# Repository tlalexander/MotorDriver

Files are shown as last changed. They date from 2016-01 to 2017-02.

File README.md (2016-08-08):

# MotorDriver

This is a smart brushless motor driver board capable of precision servo-control (position and velocity control) of a low cost hobby brushless motor. This is managed by use of a magnetic angle sensor, and a feedback software that runs on the motor driver's onboard 64MHz ARM CPU.

The board is still under development, but the ultimate goal of this board is to enable lower cost robotics, especially for hobbyists.

Brushless motors have excellent torque characteristics, but complexity in their control has meant that complex gear reductions are typically needed to make use of these motors. With improved precision on motion control, larger motors can be used in lieu of complex gear trains, reducing system complexity.

Essentially, this board moves a mechanical problem to a software problem.

This is specifically quite helpful in the field of ultra low cost 3D printed robotics, where simpler mechanisms enable near zero cost robots to be built at home.

This board is designed to facilitate the development of these applications, but is not itself particularly low cost. If you like the idea of good quality brushless motor control for hobbyist robotics, please fork this project, simplify the design, and flood the market with cheap clones from China.

### Note 7/8/2016:
The current board design works with some changes. I haven't published the changes yet. If you want to make one, contact me first. I'd be happy to push the changes if someone wants to make some of these.

Features (planned)
------

* At least 1kW maximum power handling (depending on FETs used; theoretical max power for this FET package is 3kW).
* Current feedback for proper current-based motor control.
* Position feedback via external magentic encoder enables full closed loop control of low cost hobby brushless motors.
* Devices can be synchronized for six wire motor control (custom windings, linear motors, etc).
* Independent control of all bridges allows for brushed motor control with an additional half H bridge for other loads.
* USB interface allows easy control from a linux PC. Serial interface allows control from embedded systems such as Arduino.
* CPU runs Arduino code for easy portability.
* Multicolor LED to indicate status.

TODO
-----

* ~~Determine necessary device pinout and add properly wired headers.~~
* ~~Finish layout of current sense section.~~
* ~~Add jumper for battery power to CPU.~~
* ~~Full design review (is everything hooked up right?).~~
* ~~Finish all layout of Board V1.~~
* ~~Produce first test version.~~
* Full board test. (in progress)
* Write firmware for device.

Media
-----
It works! Check out the sweet video:
https://www.youtube.com/watch?v=cGBqlPRFbaQ

License
-----

This project is licensed under Creative Commons Attribution-ShareAlike 4.0 International (CC BY-SA 4.0), which is available at: http://creativecommons.org/licenses/by-sa/4.0/ If you use the files, please check them carefully - they may contain errors.

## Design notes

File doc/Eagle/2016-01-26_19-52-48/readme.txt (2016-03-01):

**********************************************************
*****************Schematic Instructions  *******************
**********************************************************

To import your new Schematic file into Eagle:

1. Unzip the downloaded folder files to local directory and Start Eagle.
2. Select "File"->"Open"->"Schematic..." from the menu at the top of
   the screen.
3. Browse to your newly exported file and select the ".sch" file extension.
4. You should now see your schamtic available in Eagle.

**********************************************************
*******************  PCB Instructions  *******************
**********************************************************

To import your new BOARD file into Eagle:

1. Unzip the downloaded folder files to local directory and Start Eagle.
2. Select "File"->"Open"->"Board..." from the menu at the top of
   the screen.
3. Browse to your newly exported file and select the ".brd" file extension.
4. Planes will need to be repoured to update the polygon fills
	1. Once your board is loaded, type "ratsnest" into the command
	   line and press the Enter key.
	2. The polygons should all be filled now.
5. You should now have an image of your board available in Eagle.

**********************************************************
*******************  LIB Instructions  *******************
**********************************************************

To import your new library into Eagle:

1. Start Eagle.
2. Select "File"->"New"->"Library" from the menu.
3. In the blank library window, select "File" -> "Execute Script"
   from the menu.
5. Browse to your newly exported Eagle Script file (".scr" file extension)
6. After opening the file, the script will populate the new library.
   Layer 93 should NOT exist.
7. Use "File"->"Save" (or "Save As..") to save the library to the desired
   location in Eagle native format.

For additional information, please visit this site:
http://www.accelerated-designs.com/help/Eagle_import.html

You may also find this video helpful:
http://youtu.be/5jGuWY-Yy3Q

**********************************************************
**********************************************************
**********************************************************

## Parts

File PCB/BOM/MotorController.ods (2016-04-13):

Qty | Value | Device | Package | Parts | Digikey | Description | CAP | DATASHEETURL | MANUFACTURER_NAME | MANUFACTURER_PART_NUMBER | MOUNTTYPE | PACKAGEREFERENCE | PARTNUMBER | PIN_COUNT | POWER | PROD_ID | REFDES | RESISTANCE | ROHS | TOLERANCE | TYPE | VALUE | VDC | VENDOR | VFATIO | VRRM
6 | M20 | M20 | 1X20 | JP13, JP14, JP15, JP16, JP17, JP18 |  | This is just like the LOCK variant in that the holes are staggared by 5 mil, but except for the last two holes. They are not altered from the "standard" footprint layout. This is used for a special purpose on the layout of our Graphic LCD Backpack. Make sure you want to use this device before selecting it for you project!
2 | 04-JST-B4B-XH-A | 04-JST-B4B-XH-A | B4B-XH | X2, X4 | 455-2249-ND | JST CONNECTOR
3 | 05-JST-B5B-XH-A | 05-JST-B5B-XH-A | B5B-XH | X1, X6, X7 | 455-2270-ND | JST CONNECTOR
1 | 100nF | GRM188R72A104KA35D | CAP-0603 | CBOOT | 490-3285-1-ND |  | 0.0000001 |  | MuRata | GRM188R72A104KA35D |  |  |  |  |  |  |  |  |  |  |  |  | 100 | MuRata
1 | 470pF | CAPACITOR0603-CAP | CAP-0603 | U$5 | 490-1367-1-ND
4 | 0.22uF | CAPACITOR0805 | CAP-0805 | U$7, U$15, U$16, U$17 | 399-8049-1-ND
1 | 10uF | CAPACITOR0805 | CAP-0805 | U$4 | 587-1312-1-ND
1 | 4.7uF | GRM21BR61E475MA12L | CAP-0805 | COUT | 490-5422-1-ND |  | 0.0000047 | http://www.murata.com/products/catalog/pdf/c02e.pdf | MuRata | GRM21BR61E475MA12L |  |  |  |  |  |  |  |  |  |  |  |  | 25 | MuRata
1 | 2.2uF | C3225X7R2A225K230AB | CAP-1210 | CIN | 445-4497-1-ND |  | 0.0000022 | http://product.tdk.com/capacitor/mlcc/en/documents/mlcc%5Fcommercial%5Fmidvoltage%5Fen.pdf | TDK | C3225X7R2A225K230AB |  |  |  |  |  |  |  |  |  |  |  |  | 100 | TDK
2 |  | CAPACITOR-POLARIZED | CAP-6.5X18MM | C1, C4 | 4049PHCT-ND
1 | Value | LMR16006YDDCR | DDC0006A | U1 | 296-40294-1-ND |  |  |  | Texas Instruments | LMR16006YDDCR | SMT | DDC0006A | LMR16006YDDC | 6 |  |  | RefDes |  | Y |  | TYPE | Value
1 | 82uH | ME3220-823KLB | ME3220 | L1 |  |  |  |  | Coilcraft | ME3220-823KLB |  |  |  |  |  |  |  |  |  |  |  |  |  | Coilcraft
2 |  | RESISTOROHMITE | OHMITE_FCSL64_CURRENT_SENSE_RESISTOR | R2, R3 | FCSL64R050FERCT-ND | Resistor
1 | 770mV | DFLS1100-7 | POWERDI123 | D2 | DFLS1100DICT-ND |  |  | http://www.diodes.com/datasheets/ds30497.pdf | Diodes Inc. | DFLS1100-7 |  |  |  |  |  |  |  |  |  |  |  |  |  | Diodes Inc. | 0.77 | 100
6 | MOSFETSO-8 | MOSFETSO-8 | POWERPAK_S0-8 | AH, AL, BH, BL, CH, CL | SI7148DP-T1-E3CT-ND
6 | 4.7 | RESISTOR0402 | RES-0402 | R13, R14, R15, R16, R17, R18 | 311-4.70LRCT-ND | Resistor
6 | 33 | RESISTOR0402 | RES-0402 | R7, R8, R9, R10, R11, R12 | P33.0LCT-ND | Resistor
1 | 6.04k | CRCW04026K04FKED | RES-0402 | RFBB | 541-6.04KLCT-ND |  |  |  | Vishay-Dale | CRCW04026K04FKED |  |  |  |  | 0.063 |  |  | 6040 |  | 1 |  |  |  | Vishay-Dale
1 | 88.7k | CRCW040288K7FKED | RES-0402 | RFBT | 541-88.7KLCT-ND |  |  |  | Vishay-Dale | CRCW040288K7FKED |  |  |  |  | 0.063 |  |  | 88700 |  | 1 |  |  |  | Vishay-Dale
1 | 0R | RESISTOR0603 | RES-0603 | R1 | 311-0.0GRCT-ND | Resistor
6 |  | DIODESMA | SMA-DIODE | D1, D3, D4, D5, D6, D7, D8, D9, D10, D11, D12, D13 | SS110-TPCT-ND | Diode
1 | KMZ60_MAG_ANGLE_SENSOR | KMZ60_MAG_ANGLE_SENSOR | SO-8 | U$6 | 568-8400-1-ND
1 | OPA333D | OPA333D | SO08 | IC1 | 296-41364-1-ND | 1.8V, microPOWER CMOS OPERATIONAL AMPLIFIERS Zerø-Drift Series
1 | HIP4086_HEX_MOSFET_DRIVER | HIP4086_HEX_MOSFET_DRIVER | SOIC-24 | U$3 | HIP4086ABZ-ND
4 | STAND-OFF | STAND-OFF | STAND-OFF | STANDOFF1, STANDOFF2, STANDOFF3, STANDOFF4 |  | #4 Stand Off
14 | TEST_POINT5015KCT-ND | TEST_POINT5015KCT-ND | TEST_POINT_SMT_KEYSTONE_5015 | TP1, TP2, TP3, TP4, TP5, TP6, TP7, TP8, TP9, TP11, TP12, TP13, TP14, TP15 | 36-5015CT-ND | 36-5015CT-ND
1 | USBPTH | USBPTH | USB-B-PTH | X5 |  | USB Connectors

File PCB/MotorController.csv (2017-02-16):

Qty | Value | Device | Package | Parts | Description | CAP | COMPTYPE | DATASHEETURL | DCR | ESR | IDC | IO | IRMS | L | MANUFACTURER | MANUFACTURER_NAME | MANUFACTURER_PART_NUMBER | MOUNTTYPE | PACKAGEREFERENCE | PARTNUMBER | PIN_COUNT | POWER | PROD_ID | REFDES | RESISTANCE | ROHS | TOLERANCE | TYPE | VALUE | VDC | VENDOR | VFATIO | VRRM
2 |  | CAPACITOR-POLARIZED | CAP-6.5X18MM | C1, C4
6 |  | DIODESMA | SMA-DIODE | D1, D3, D4, D5, D6, D7 | Diode
1 |  | DIODESOD123 | SOD-123 | D14 | Diode
1 |  | M01PTH | 1X01 | J1 | Header 1
1 |  | M02PTH | 1X02 | J2 | Standard 2-pin 0.1 header. Use with"
2 |  | RESISTOR0603 | 0603-RES | R22, R23 | Resistor
2 |  | RESISTOROHMITE | OHMITE_FCSL64_CURRENT_SENSE_RESISTOR | R2, R3 | Resistor
3 | 0.22uF | CAPACITOR0805 | 0808-CAP | U$15, U$16, U$17
2 | 04-JST-B4B-XH-A | 04-JST-B4B-XH-A | B4B-XH | X2, X4 | JST CONNECTOR
2 | 05-JST-B5B-XH-A | 05-JST-B5B-XH-A | B5B-XH | X1, X7 | JST CONNECTOR
1 | 0R | RESISTOR0603 | 0603-RES | R1 | Resistor
1 | 100nF | GRM188R72A104KA35D | 0603 | CBOOT |  | 1.0E-7 |  |  |  | 0.0 |  |  | 0.0 |  |  | MuRata | GRM188R72A104KA35D |  |  |  |  |  |  |  |  |  |  |  |  | 100.0 | MuRata
1 | 10uF | CAPACITOR0805 | 0808-CAP | U$4
1 | 2.2uF | C3225X7R2A225K230AB | 1210 | CIN |  | 2.2E-6 |  | http://product.tdk.com/capacitor/mlcc/en/documents/mlcc%5Fcommercial%5Fmidvoltage%5Fen.pdf |  | 0.0028 |  |  | 9.824718 |  |  | TDK | C3225X7R2A225K230AB |  |  |  |  |  |  |  |  |  |  |  |  | 100.0 | TDK
3 | 20k | RESISTOR0402 | 0402-RES | R19, R20, R21 | Resistor
6 | 33 | RESISTOR0402 | 0402-RES | R7, R8, R9, R10, R11, R12 | Resistor
3 | 4.7 | RESISTOR0402 | 0402-RES | R13, R14, R15 | Resistor
1 | 4.7uF | GRM21BR61E475MA12L | 0805 | COUT |  | 4.7E-6 |  | http://www.murata.com/products/catalog/pdf/c02e.pdf |  | 0.0020 |  |  | 7.29 |  |  | MuRata | GRM21BR61E475MA12L |  |  |  |  |  |  |  |  |  |  |  |  | 25.0 | MuRata
1 | 470pF | CAPACITOR0603-CAP | 0603-CAP | U$5
1 | 6.04k | CRCW04026K04FKED | 0402 | RFBB |  |  |  |  |  |  |  |  |  |  |  | Vishay-Dale | CRCW04026K04FKED |  |  |  |  | 0.063 |  |  | 6040.0 |  | 1.0 |  |  |  | Vishay-Dale
1 | 6.04k | RESISTOR0402 | 0402-RES | R18 | Resistor
1 | 770mV | DFLS1100-7 | POWERDI123 | D2 |  |  |  | http://www.diodes.com/datasheets/ds30497.pdf |  |  |  | 1.0 |  |  |  | Diodes Inc. | DFLS1100-7 |  |  |  |  |  |  |  |  |  |  |  |  |  | Diodes Inc. | 0.77 | 100.0
1 | 7805TV | 7805TV | TO220V | IC2 | Positive VOLTAGE REGULATOR
1 | 82uH | ME3220-823KLB | ME3220 | L1 |  |  |  |  | 3.0 |  | 0.34 |  |  | 8.2E-5 |  | Coilcraft | ME3220-823KLB |  |  |  |  |  |  |  |  |  |  |  |  |  | Coilcraft
1 | 88.7K | RESISTOR0402 | 0402-RES | R17 | Resistor
1 | 88.7k | CRCW040288K7FKED | 0402 | RFBT |  |  |  |  |  |  |  |  |  |  |  | Vishay-Dale | CRCW040288K7FKED |  |  |  |  | 0.063 |  |  | 88700.0 |  | 1.0 |  |  |  | Vishay-Dale
1 | DNS | RESISTOR0402 | 0402-RES | R16 | Resistor
1 | DNS | RESISTOR0603 | 0603-RES | R4 | Resistor
1 | FILT_C | CAP0805 | 0805 | R6 | Capacitor
1 | FILT_R | RESISTOR0603 | 0603-RES | R5 | Resistor
5 | HIGHCURRENTPAD2 | HIGHCURRENTPAD2 | HIGH_CURRENT_PAD2 | +, -, A, B, C
1 | HIP4086_HEX_MOSFET_DRIVER | HIP4086_HEX_MOSFET_DRIVER | SOIC-24 | U$3
6 | M20 | M20 | 1X20 | JP13, JP14, JP15, JP16, JP17, JP18 | This is just like the LOCK variant in that the holes are staggared by 5 mil, but except for the last two holes. They are not altered from the standard" footprint layout. This is used for a special purpose on the layout of our Graphic LCD Backpack. Make sure you want to use this device before selecting it for you project!"
6 | MBRA140 | DIODE-SCHOTTKY-MBRA140 | SMA-DIODE | D8, D9, D10, D11, D12, D13 | Schottky diodes in SFE's production catalog |  |  |  |  |  |  |  |  |  |  |  |  |  |  |  |  |  | DIO-08053 |  |  |  |  |  | MBRA140
6 | MOSFETSO-8 | MOSFETSO-8 | POWERPAK_S0-8 | AH, AL, BH, BL, CH, CL
1 | MOSFETSOT23 | MOSFETSOT23 | SOT23 | U$1
1 | OPA333D | OPA333D | SO08 | IC1 | 1.8V, microPOWER CMOS OPERATIONAL AMPLIFIERS Zerø-Drift Series
1 | SOLDERJUMPERNO | SOLDERJUMPERNO | SJ_2S-NO | SJ1 | Solder Jumper
4 | STAND-OFF | STAND-OFF | STAND-OFF | STANDOFF1, STANDOFF2, STANDOFF3, STANDOFF4 | #4 Stand Off
14 | TEST_POINT5015KCT-ND | TEST_POINT5015KCT-ND | TEST_POINT_SMT_KEYSTONE_5015 | TP1, TP2, TP3, TP4, TP5, TP6, TP7, TP8, TP9, TP11, TP12, TP13, TP14, TP15 | Test Points. First one is Keystone
1 | USBPTH | USBPTH | USB-B-PTH | X5 | USB Connectors
1 | Value | LMR16006YDDCR | DDC0006A | U1 |  |  | IC |  |  |  |  |  |  |  | Texas Instruments | Texas Instruments | LMR16006YDDCR | SMT | DDC0006A | LMR16006YDDC | 6 |  |  | RefDes |  | Y |  | TYPE | Value

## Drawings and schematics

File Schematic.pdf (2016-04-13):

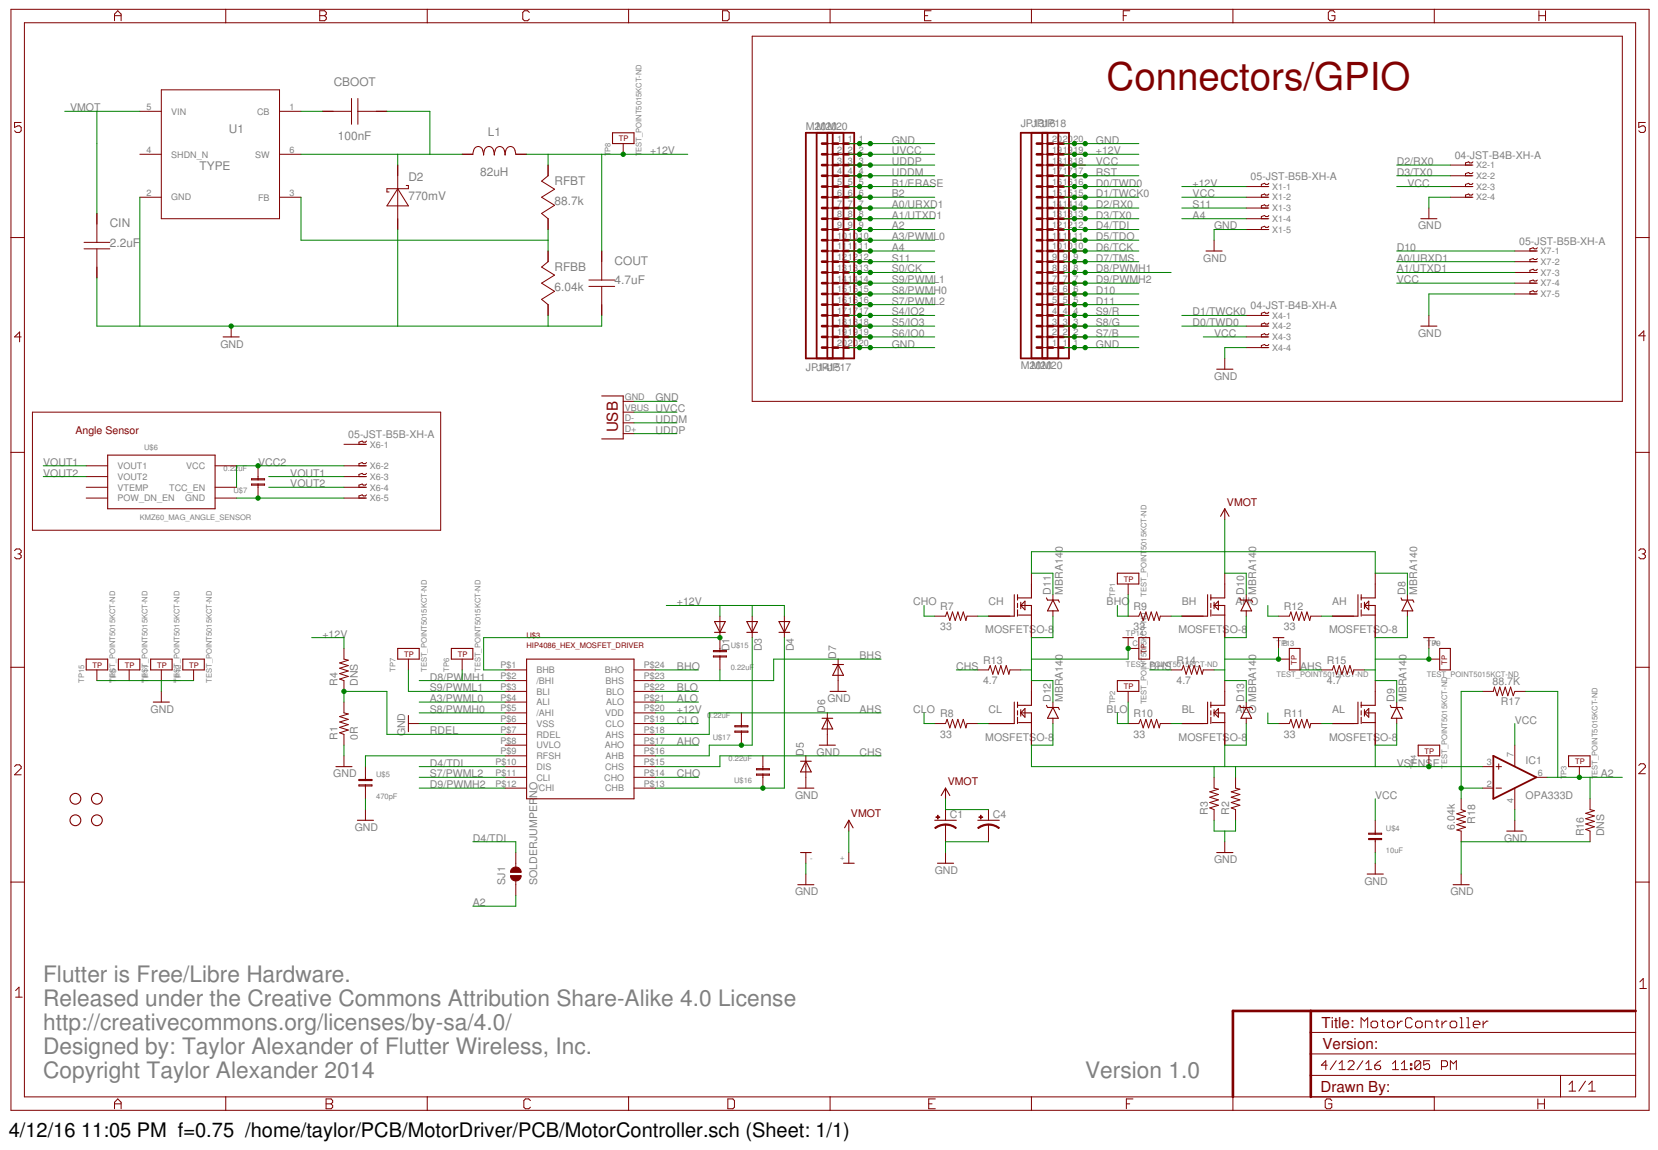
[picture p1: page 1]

Flutter is Free/Libre Hardware. Released under the Creative Commons Attribution Share-Alike 4.0 License
http://creativecommons.org/licenses/by-sa/4.0/

Drawn By: Title: Version:

4/12/16 11:05 PM f=0.75 /home/taylor/PCB/MotorDriver/PCB/MotorController.sch (Sheet: 1/1)

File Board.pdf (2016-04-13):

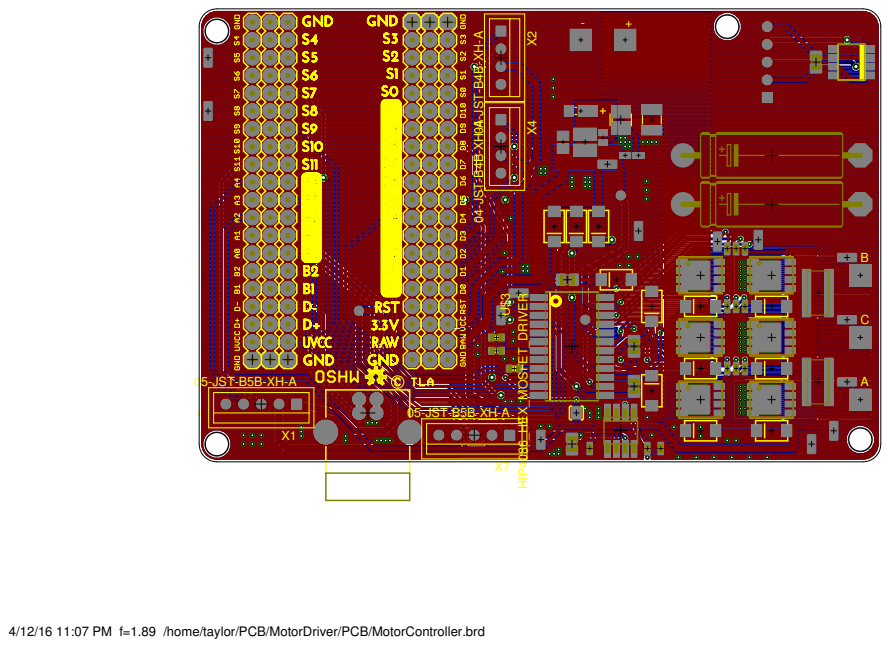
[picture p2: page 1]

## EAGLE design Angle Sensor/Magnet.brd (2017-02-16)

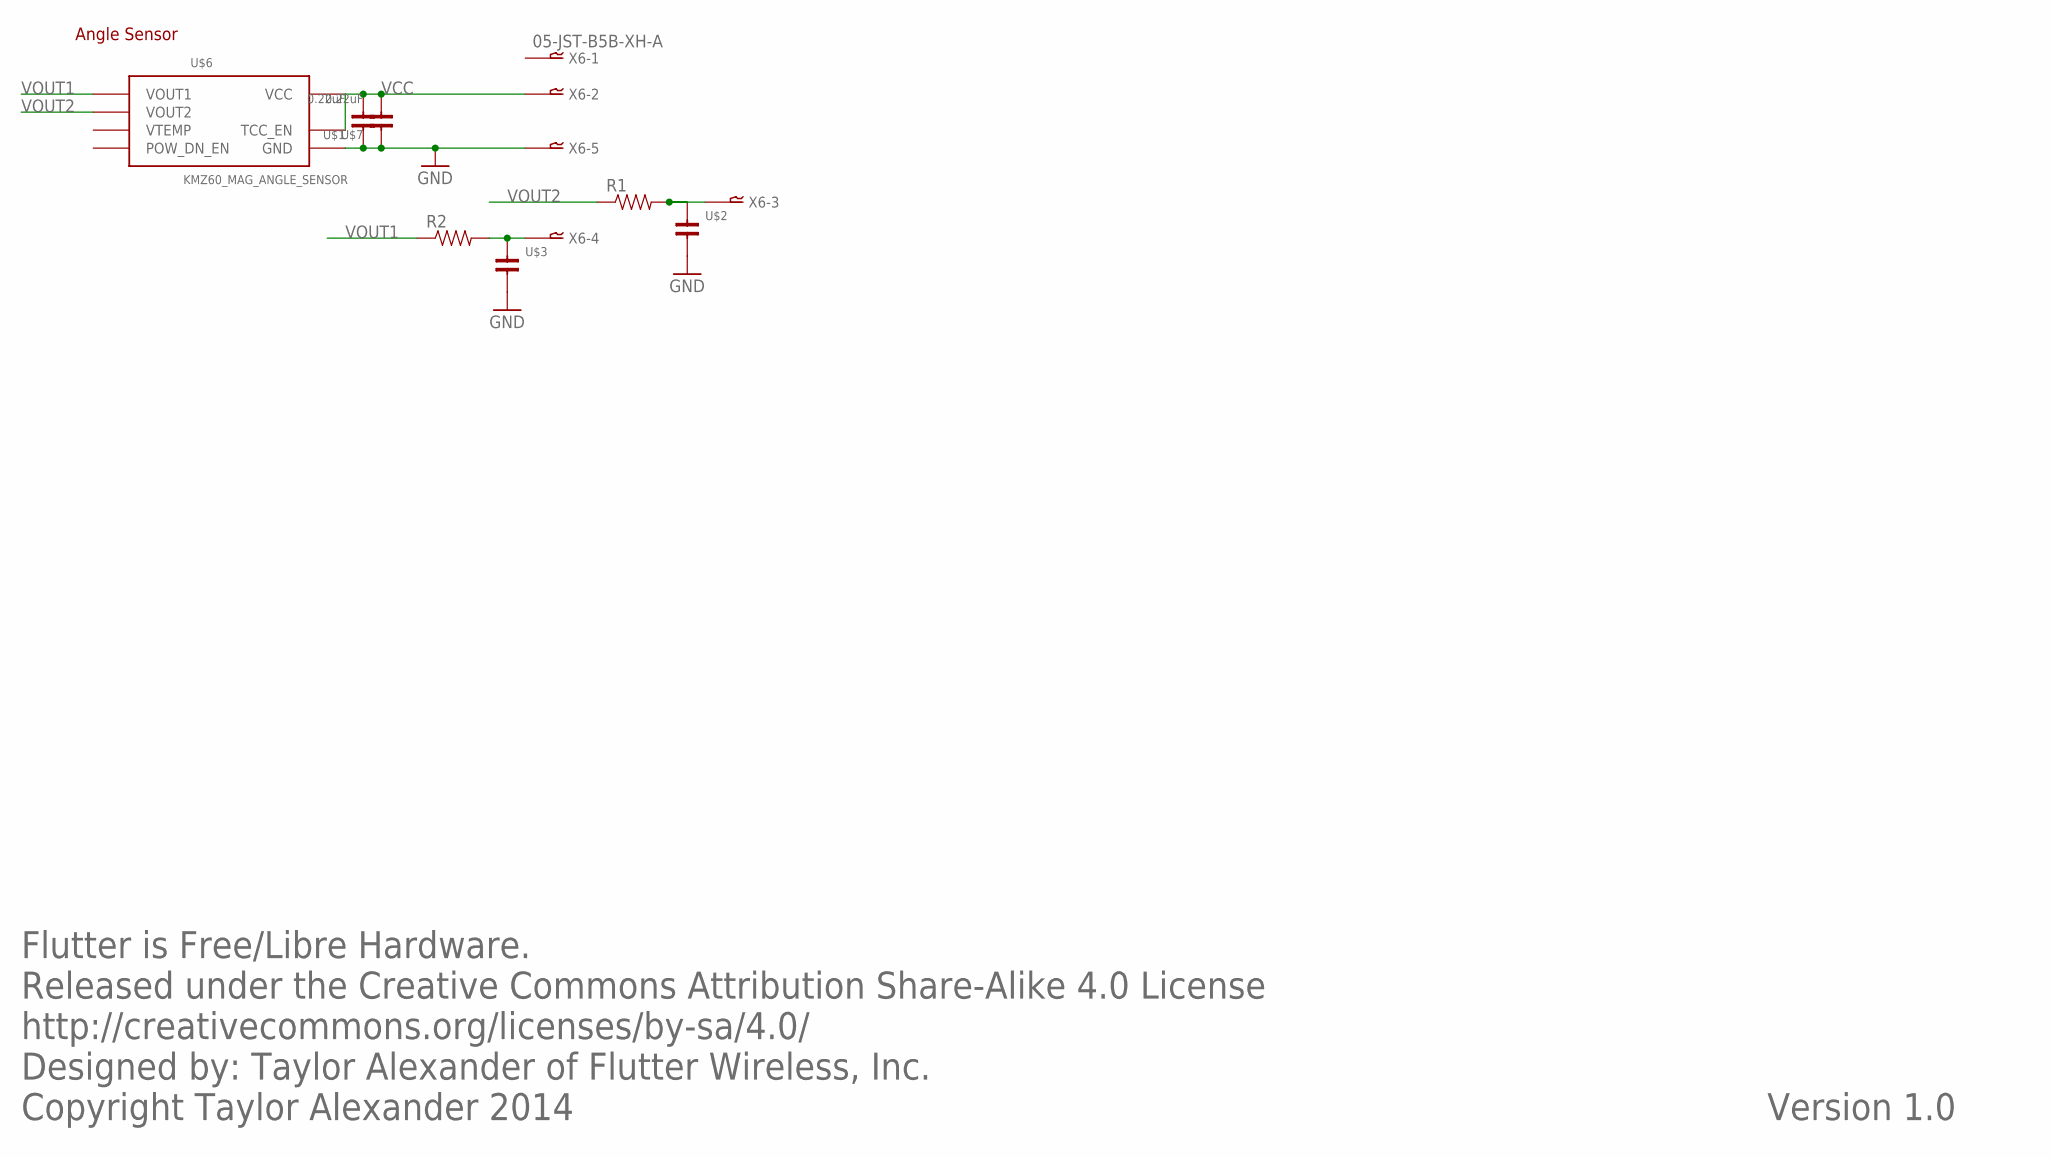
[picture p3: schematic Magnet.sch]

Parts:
R1, R2: RESISTOR0603; 0603-RES
U$1, U$7: 0.22uF; 0808-CAP
U$2, U$3: CAPACITOR0603-CAP; 0603-CAP
U$6: KMZ60_MAG_ANGLE_SENSOR; SO-8
X6: 05-JST-B5B-XH-A; B5B-XH

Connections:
GND: U$1.1, U$2.2, U$3.2, U$6.P$3 (GND), U$6.P$6 (GND), U$7.1, X6.P$5
unnamed: R2.2, U$3.1, X6.P$4
unnamed: R1.2, U$2.1, X6.P$3
VCC: U$1.2, U$6.P$1 (TCC_EN), U$6.P$7 (VCC), U$7.2, X6.P$2
VOUT1: R2.1, U$6.P$2 (VOUT1)
VOUT2: R1.1, U$6.P$4 (VOUT2)

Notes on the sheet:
Flutter is Free/Libre Hardware. Released under the Creative Commons Attribution Share-Alike 4.0 License http://creativecommons.org/licenses/by-sa/4.0/ Designed by: Taylor Alexander of Flutter Wireless, Inc. Copyright Taylor Alexander 2014
Version 1.0
Angle Sensor

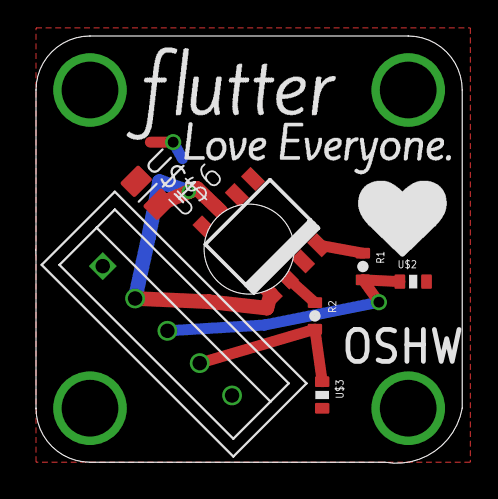
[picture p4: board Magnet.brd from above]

Board: 2 copper layers, 23.7 x 23.7 mm, 8 parts (1 on the bottom side), 6 nets.

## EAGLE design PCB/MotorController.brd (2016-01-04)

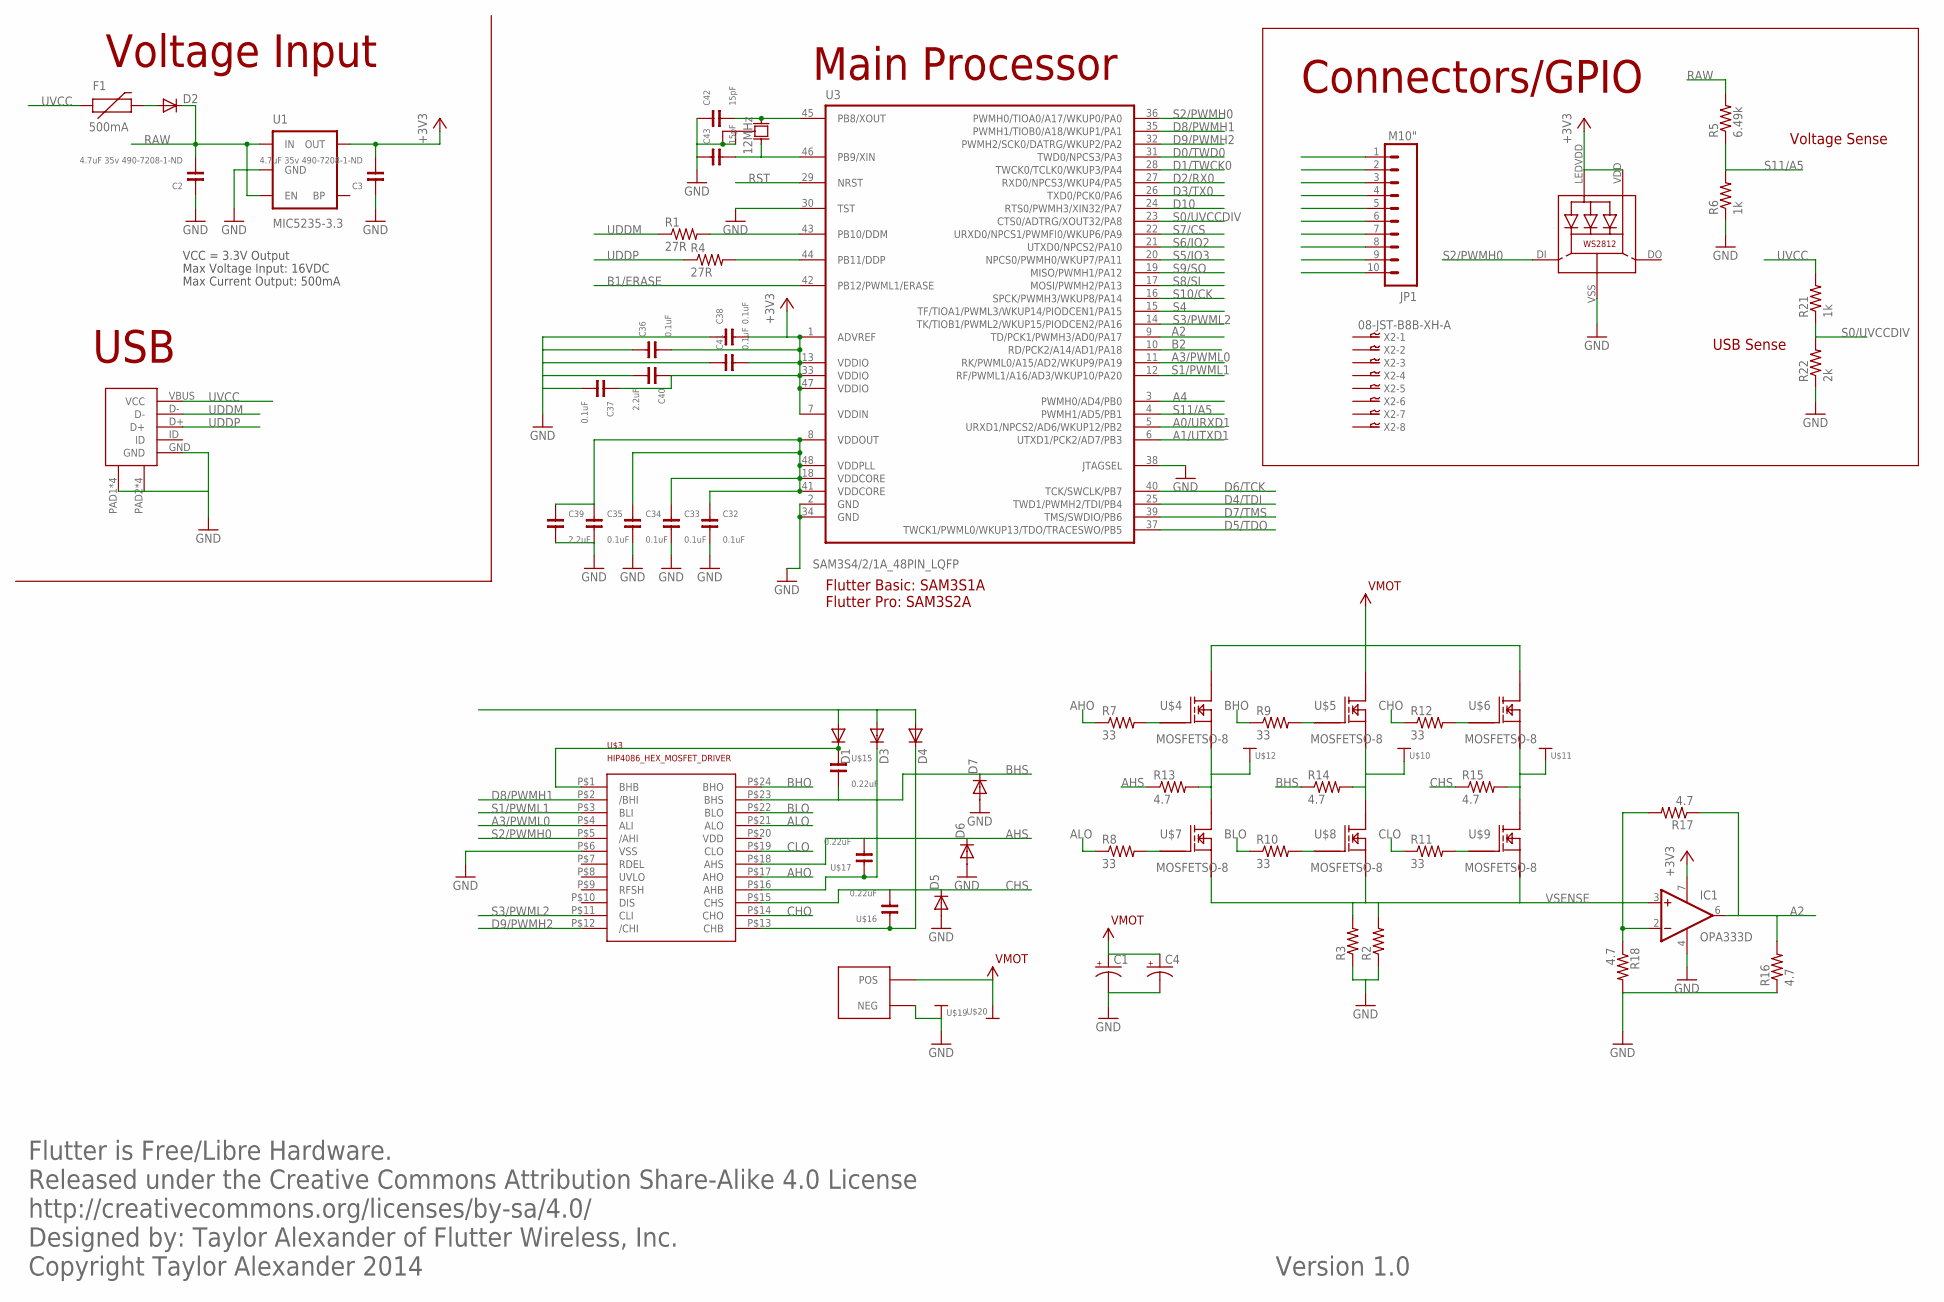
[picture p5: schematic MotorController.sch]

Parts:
C1, C4: CAPACITOR-POLARIZED; CAP-6.5X18MM
C2, C3: 4.7uF 35v 490-7208-1-ND; 0808-CAP
C32, C33, C34, C35, C36, C37, C38, C41: 0.1uF; 0402-CAP
C39, C40: 2.2uF; 0402-CAP
C42, C43: 15pF; 0402-CAP
D1, D3, D4, D5, D6, D7: DIODESMA; SMA-DIODE
D2: DIODESOD; SOD-323
F1: 500mA; 0603-PTC
IC1: OPA333D; SO08
JP1: M10"; 1X10
LED1: WS2812
R1, R4: 27R; 0402-RES
R2, R3: RESISTOROHMITE; OHMITE_FCSL64_CURRENT_SENSE_RESISTOR
R5: 6.49k; 0402-RES
R6, R21: 1k; 0402-RES
R7, R8, R9, R10, R11, R12: 33; 0402-RES
R13, R14, R15, R16, R17, R18: 4.7; 0402-RES
R22: 2k; 0402-RES
U1: MIC5235-3.3; SOT23-5
U3: SAM3S4/2/1A_48PIN_LQFP; LQFP48
U$2: MICRO_USB; MICRO-USB-SLOT-2
U$3: HIP4086_HEX_MOSFET_DRIVER; SOIC-24
U$4, U$5, U$6, U$7, U$8, U$9: MOSFETSO-8; POWERPAK_S0-8
U$10, U$11, U$12, U$19, U$20: HIGHCURRENTPAD2; HIGH_CURRENT_PAD2
U$15, U$16, U$17: 0.22uF; 0808-CAP
U$21: XT60; XT60_CONNECTOR
X1: 12MHz; XTAL_ABRACON_ABM8G_3.2MMX2.5MM
X2: 08-JST-B8B-XH-A; B8B-XH

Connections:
3.3V: C3.2, C36.2, C37.1, C38.2, C40.1, C41.2, U1.5 (OUT), U3.1 (ADVREF), U3.7 (VDDIN), U3.13 (VDDIO), U3.33 (VDDIO), U3.47 (VDDIO)
+1.8V: C32.1, C33.1, C34.1, C35.1, C39.1, U3.8 (VDDOUT), U3.18 (VDDCORE), U3.41 (VDDCORE), U3.48 (VDDPLL)
+3V3: IC1.7 (V+), LED1.LEDVDD, LED1.VDD
A: R15.2, U$6.S@1 (S), U$6.S@2 (S), U$6.S@3 (S), U$9.D@1 (D), U$9.D@2 (D), U$9.D@3 (D), U$9.D@4 (D), U$9.DTOP (D), U$11.P$1
A0/URXD1: U3.5 (URXD1/NPCS2/AD6/WKUP12/PB2)
A1/UTXD1: U3.6 (UTXD1/PCK2/AD7/PB3)
A2: IC1.6 (OUT), R16.2, R17.1, U3.9 (TD/PCK1/PWMH3/AD0/PA17)
A3/PWML0: U3.11 (RK/PWML0/A15/AD2/WKUP9/PA19), U$3.P$4 (ALI)
A4: U3.3 (PWMH0/AD4/PB0)
AHO: R7.1, U$3.P$17 (AHO)
AHS: D6.C, R13.1, U$3.P$18 (AHS), U$17.2
ALO: R8.1, U$3.P$21 (ALO)
B: R13.2, U$4.S@1 (S), U$4.S@2 (S), U$4.S@3 (S), U$7.D@1 (D), U$7.D@2 (D), U$7.D@3 (D), U$7.D@4 (D), U$7.DTOP (D), U$12.P$1
B1/ERASE: U3.42 (PB12/PWML1/ERASE)
B2: U3.10 (RD/PCK2/A14/AD1/PA18)
BHO: R9.1, U$3.P$24 (BHO)
BHS: D7.C, R14.1, U$3.P$23 (BHS), U$15.2
BLO: R10.1, U$3.P$22 (BLO)
C: R14.2, U$5.S@1 (S), U$5.S@2 (S), U$5.S@3 (S), U$8.D@1 (D), U$8.D@2 (D), U$8.D@3 (D), U$8.D@4 (D), U$8.DTOP (D), U$10.P$1
CHO: R12.1, U$3.P$14 (CHO)
CHS: D5.C, R15.1, U$3.P$15 (CHS), U$16.2
CLO: R11.1, U$3.P$19 (CLO)
D0/TWD0: U3.31 (TWD0/NPCS3/PA3)
D1/TWCK0: U3.28 (TWCK0/TCLK0/WKUP3/PA4)
D2/RX0: U3.27 (RXD0/NPCS3/WKUP4/PA5)
D3/TX0: U3.26 (TXD0/PCK0/PA6)
D4/TDI: U3.25 (TWD1/PWMH2/TDI/PB4)
D5/TDO: U3.37 (TWCK1/PWML0/WKUP13/TDO/TRACESWO/PB5)
D6/TCK: U3.40 (TCK/SWCLK/PB7)
D7/TMS: U3.39 (TMS/SWDIO/PB6)
D8/PWMH1: U3.35 (PWMH1/TIOB0/A18/WKUP1/PA1), U$3.P$2 (/BHI)
D9/PWMH2: U3.32 (PWMH2/SCK0/DATRG/WKUP2/PA2), U$3.P$12 (/CHI)
D10: U3.24 (RTS0/PWMH3/XIN32/PA7)
GND: C1.-, C2.1, C3.1, C4.-, C32.2, C33.2, C34.2, C35.2, C36.1, C37.2, C38.1, C39.2, C40.2, C41.1, C42.1, C43.1, D5.A, D6.A, D7.A, IC1.4 (V-), LED1.VSS (GND), R2.P$1 (1), R3.P$1 (1), R6.1, R16.1, R18.2, R22.1, U1.2 (GND), U3.2 (GND), U3.30 (TST), U3.34 (GND), U3.38 (JTAGSEL), U$2.GND, U$2.PAD1, U$2.PAD2, U$2.PAD3, U$2.PAD4, U$2.PAD5, U$2.PAD6, U$2.PAD7, U$2.PAD8, U$3.P$6 (VSS), U$19.P$1, U$21.P$2 (NEG), X1.P$2 (GND), X1.P$4 (GND)
unnamed: D3.C, U$3.P$16 (AHB), U$17.1
unnamed: D1.A, D3.A, D4.A
unnamed: IC1.2 (-IN), R17.2, R18.1
unnamed: R7.2, U$4.G
unnamed: R8.2, U$7.G
unnamed: D2.2 (A), F1.2
unnamed: R9.2, U$5.G
unnamed: R10.2, U$8.G
unnamed: R11.2, U$9.G
unnamed: R12.2, U$6.G
unnamed: D1.C, U$3.P$1 (BHB), U$15.1
unnamed: D4.C, U$3.P$13 (CHB), U$16.1
unnamed: C42.2, U3.45 (PB8/XOUT), X1.P$3 (X2)
unnamed: C43.2, U3.46 (PB9/XIN), X1.P$1 (X1)
RAW: C2.2, D2.1 (C), R5.2, U1.1 (IN), U1.3 (EN)
RST: U3.29 (NRST)
S0/UVCCDIV: R21.1, R22.2, U3.23 (CTS0/ADTRG/XOUT32/PA8)
S1/PWML1: U3.12 (RF/PWML1/A16/AD3/WKUP10/PA20), U$3.P$3 (BLI)
S2/PWMH0: LED1.DI, U3.36 (PWMH0/TIOA0/A17/WKUP0/PA0), U$3.P$5 (/AHI)
S3/PWML2: U3.14 (TK/TIOB1/PWML2/WKUP15/PIODCEN2/PA16), U$3.P$11 (CLI)
S4: U3.15 (TF/TIOA1/PWML3/WKUP14/PIODCEN1/PA15)
S5/IO3: U3.20 (NPCS0/PWMH0/WKUP7/PA11)
S6/IO2: U3.21 (UTXD0/NPCS2/PA10)
S7/CS: U3.22 (URXD0/NPCS1/PWMFI0/WKUP6/PA9)
S8/SI: U3.17 (MOSI/PWMH2/PA13)
S9/SO: U3.19 (MISO/PWMH1/PA12)
S10/CK: U3.16 (SPCK/PWMH3/WKUP8/PA14)
S11/A5: R5.1, R6.2, U3.4 (PWMH1/AD5/PB1)
UDDC_+: R4.2, U3.44 (PB11/DDP)
UDDC_-: R1.2, U3.43 (PB10/DDM)
UDDM: R1.1, U$2.D-
UDDP: R4.1, U$2.D+
UVCC: F1.1, R21.2, U$2.VBUS (VCC)
VMOT: C1.+, C4.+, U$4.D@1 (D), U$4.D@2 (D), U$4.D@3 (D), U$4.D@4 (D), U$4.DTOP (D), U$5.D@1 (D), U$5.D@2 (D), U$5.D@3 (D), U$5.D@4 (D), U$5.DTOP (D), U$6.D@1 (D), U$6.D@2 (D), U$6.D@3 (D), U$6.D@4 (D), U$6.DTOP (D), U$20.P$1, U$21.P$1 (POS)
VSENSE: IC1.3 (+IN), R2.P$2 (2), R3.P$2 (2), U$7.S@1 (S), U$7.S@2 (S), U$7.S@3 (S), U$8.S@1 (S), U$8.S@2 (S), U$8.S@3 (S), U$9.S@1 (S), U$9.S@2 (S), U$9.S@3 (S)

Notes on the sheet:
Max Voltage Input: 16VDC
Max Current Output: 500mA
VCC = 3.3V Output
Flutter is Free/Libre Hardware. Released under the Creative Commons Attribution Share-Alike 4.0 License http://creativecommons.org/licenses/by-sa/4.0/ Designed by: Taylor Alexander of Flutter Wireless, Inc. Copyright Taylor Alexander 2014
Voltage Input
Main Processor
Connectors/GPIO
USB
Flutter Basic: SAM3S1A Flutter Pro: SAM3S2A
Voltage Sense
USB Sense
Version 1.0

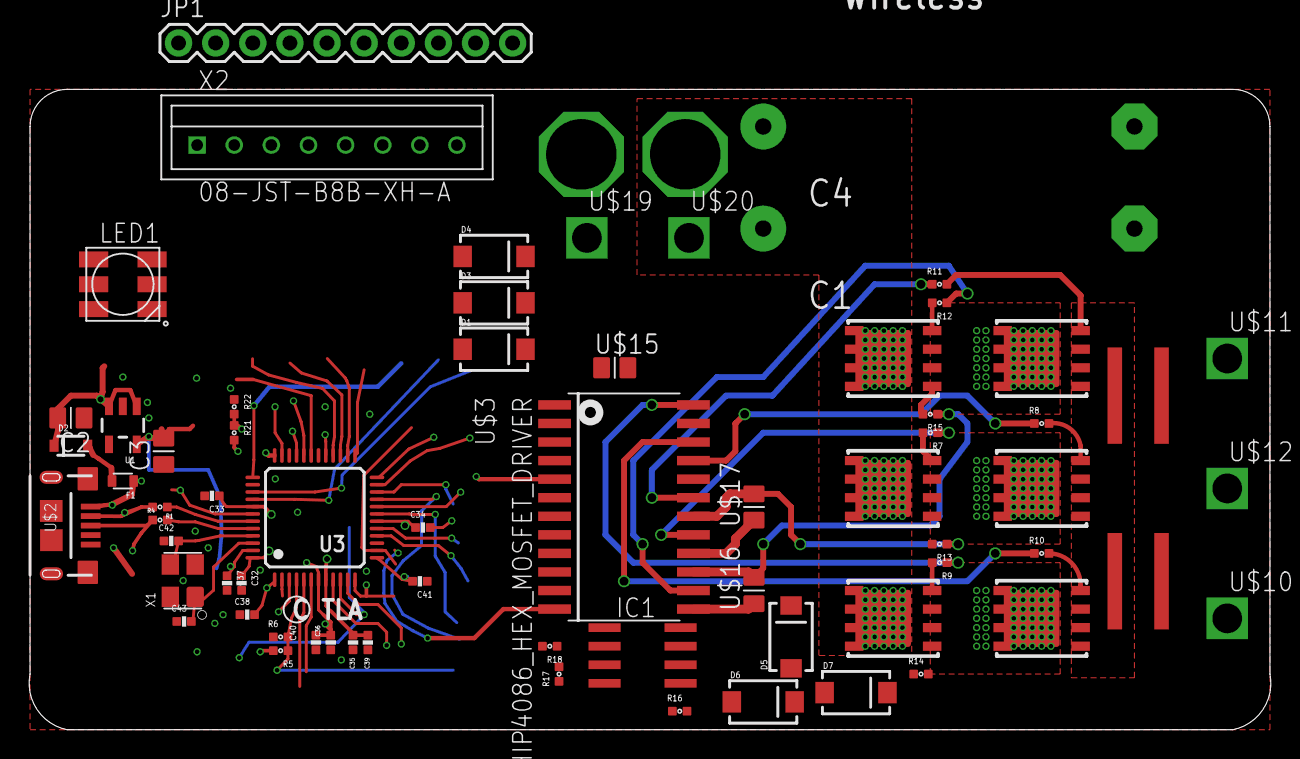
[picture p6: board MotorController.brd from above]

Board: 4 copper layers, 84.9 x 43.8 mm, 69 parts (0 on the bottom side), 47 nets.

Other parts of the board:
U$1: OSHW-LOGOS; OSHW-LOGO-S

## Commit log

2016-01-04 Move current sense circuit around, update readme
    [MotorController.brd]
2016-03-01 Added 12v power supply, removed CPU in favor of Flutter (for quick development), added headers... many other changes. This commit represents version 0.1 of the hardware.
    [2016-01-26_19-52-48.sch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]
2016-04-13 Added BOM, Added PDFs of Schematic and PCB, Updated Project Status in Readme, added video to Readme
    [MotorController.ods, MotorController.sch]
2016-08-08 Updated readme. Also pushing latest changes to board. Can't actually remember what they are.
    [MotorController.sch]
2016-09-05 Updated wiring for better compatibility with Flutter, fixed current sense filter, removed angle sensor.
    [MotorController.sch]
2017-02-16 Added angle sensor. Checked in latest board version.
    [Magnet.GBL, Magnet.GBO, Magnet.GBS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]
